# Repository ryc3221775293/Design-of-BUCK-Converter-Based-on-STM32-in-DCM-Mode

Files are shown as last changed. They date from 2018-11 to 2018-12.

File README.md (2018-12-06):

# 基于STM32的DCM模式下的BUCK变换器设计

- 本工程包括软件部分的STM32的代码以及硬件部分的Altium Designer设计的PCB
- STM32使用STM32F103RCT6并移植FreeRTOS操作系统，进行按键任务、ADC任务、PWM生成任务、PID任务的调度管理
- PCB包括控制电路STM32，驱动电路以及主电路BUCK电路

下面就两部分进行介绍：

## 5、硬件部分

### 5.1、STM32F103RCT6控制电路

Cortex-M3采用目前主流ARM V7-M架构，相比曾风靡一时的ARM V4T架构拥有更加强劲的性能，更高的代码密度，更高的性价比。Cortex-M3处理器结合多种突破性技术，在低功耗、低成本、高性能三方面具有突破性的创新，使其在这几年迅速在中低端单片机市场异军突起。

国内Cortex-M3市场，ST（意法半导体）公司的STM32无疑是最大赢家，作为Cortex-M3内核最先尝蟹的两个公司（另一个是Luminary（流明））之一，ST无论是在市场占有率，还是在技术支持方面，都是远超其他对手。在Cortex-M3芯片的选择上，STM32无疑是大家的首选。所以自从ST推出STM32之后，一股强劲的STM32学习开发风潮扑面而来。本书也因STM32的流行应运而生。

开发板选择的是STM32F103RCT6作为MCU，它拥有的资源包括：48KBSRAM、256KBFLASH、2个基本定时器、4个通用定时器、2个高级定时器、2个DMA控制器（共12个通道）、3个SPI、2个IIC、5个串口、1个USB、1个CAN、3个12位ADC、1个12位DAC、1个SDIO接口及51个通用IO口。该芯片性价比极高。

#### 5.1.1 MCU部分的原理图如图

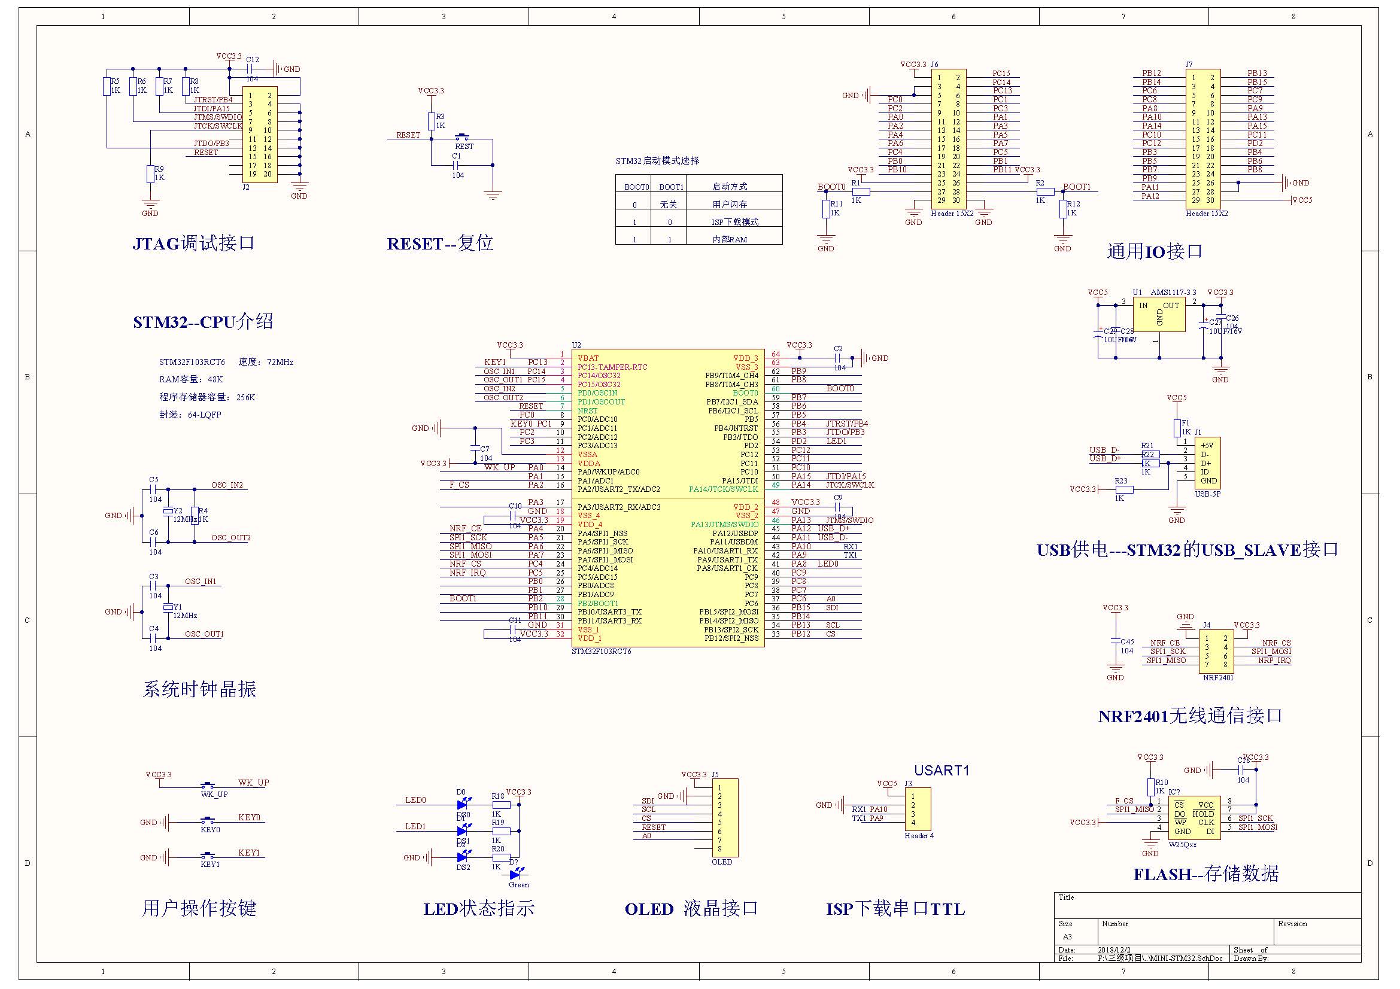
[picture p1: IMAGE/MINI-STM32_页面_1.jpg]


#### 5.1.2 PCB如图

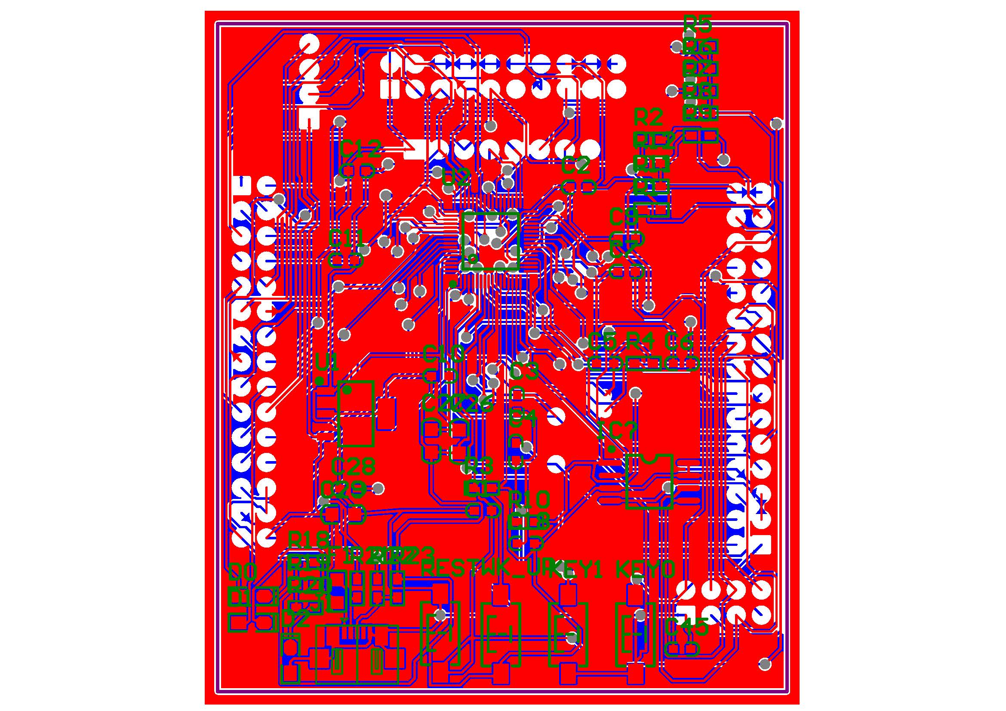
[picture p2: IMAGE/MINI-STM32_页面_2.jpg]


#### 5.1.3 PCB板的3D效果如图

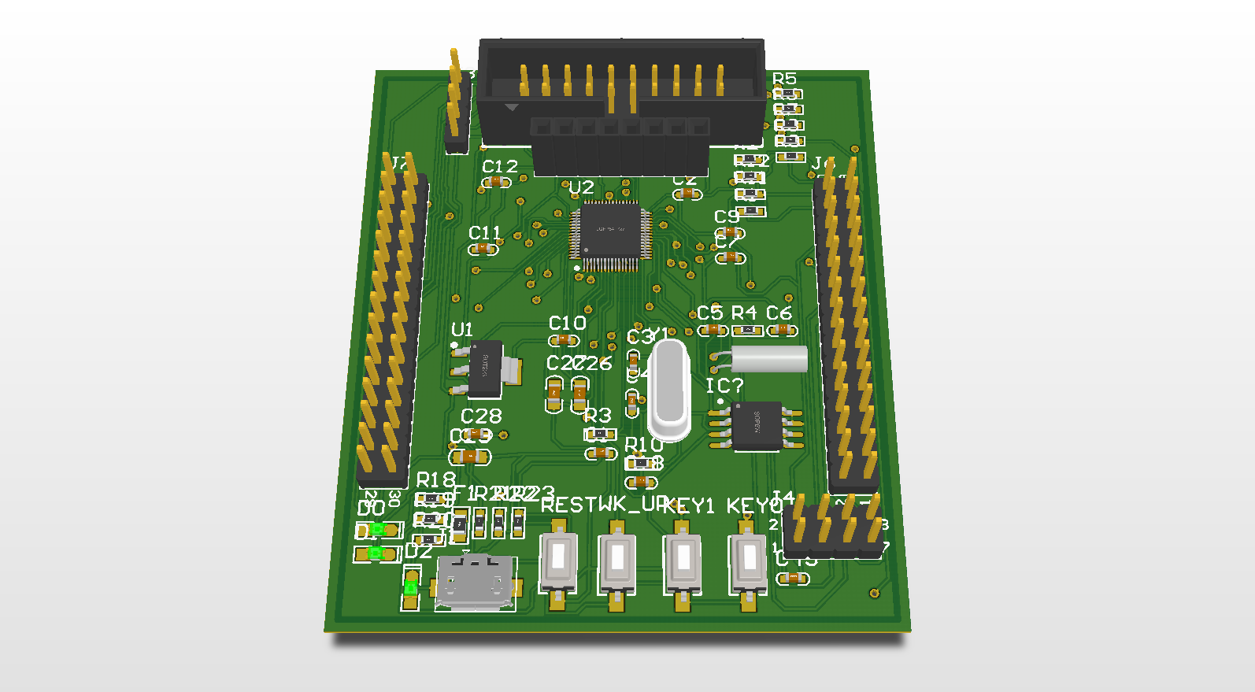
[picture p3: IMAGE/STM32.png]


#### 5.1.4 BOM报表如下

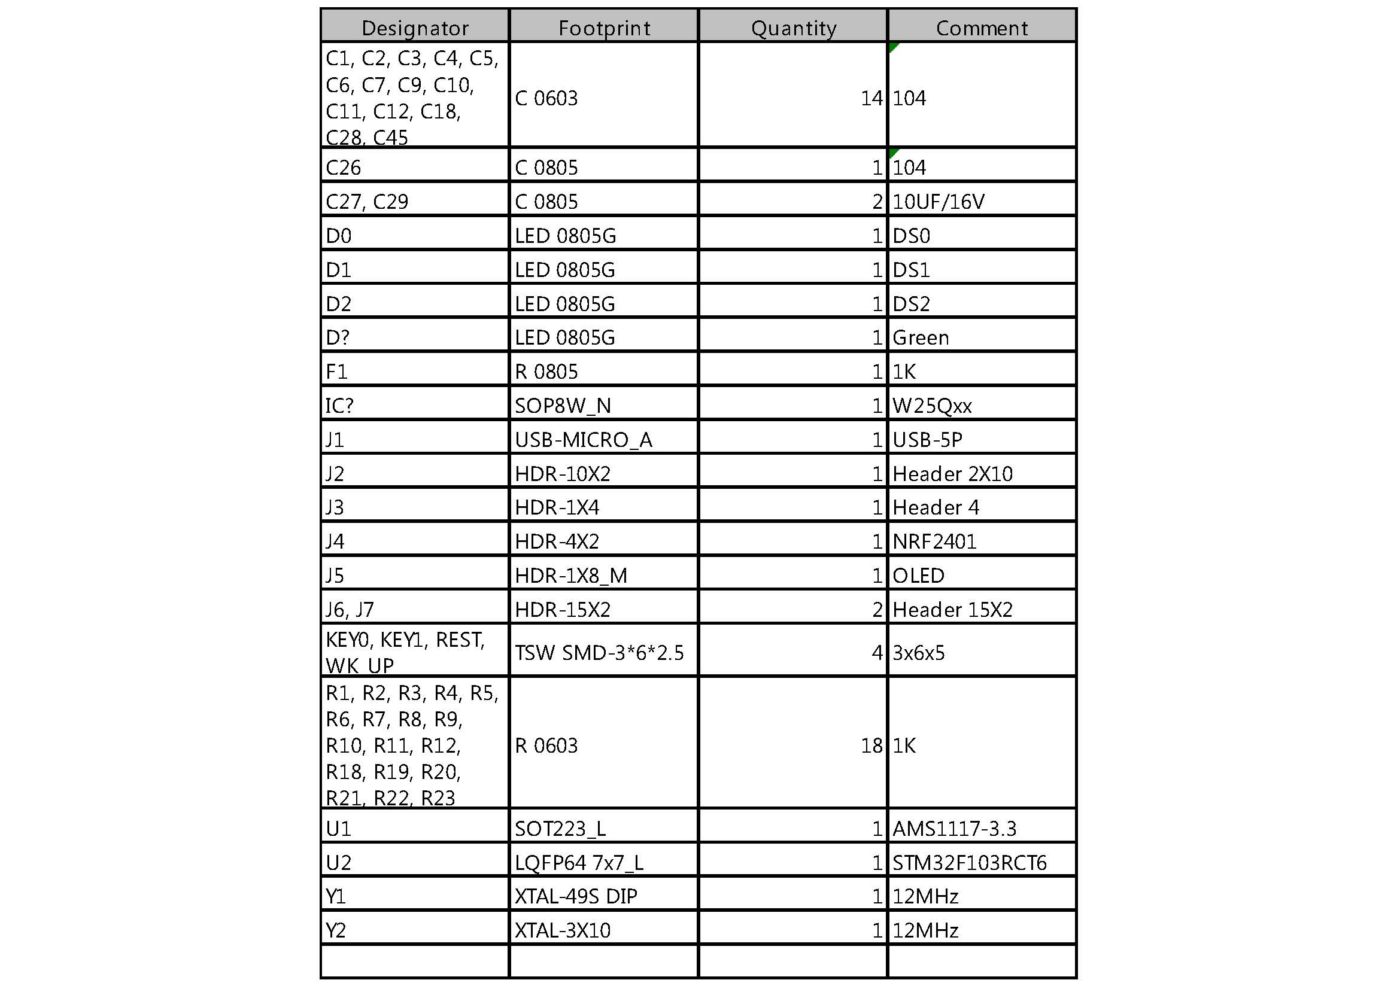
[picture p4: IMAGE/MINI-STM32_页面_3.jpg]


上图中中上部的BOOT1用于设置STM32的启动方式，其对应启动模式如下表所示：

| BOOT0 | BOOT1 | 启动模式 | 说明 |
| :---: | :---: | :---: | :---: |
| 0 | X | 用户闪存存储器 | 用户闪存存储器，也就是FLASH启动 |
| 1 | 0 | 系统存储器 |  系统存储器启动，用于串口下载 |
| 1 | 1 | SRAM启动 | SRAM启动，用于在SRAM中调试代码  |

一般情况下（即标准的ISP下载步骤）如果我们想用用串口下载代码，则必须先配置BOOT0为1，BOOT1为0，然后按复位键，最后再通过程序下载代码，下载完以后又需要将BOOT0设置为GND，以便每次复位后都可以运行用户代码。

#### 5.1.5 JTAG部分电路如下图：

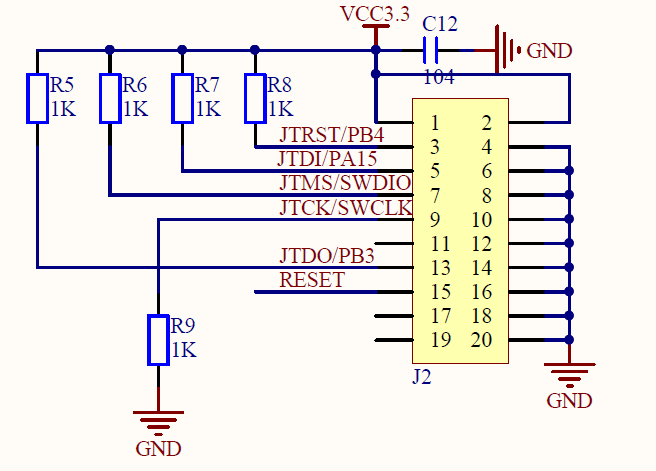
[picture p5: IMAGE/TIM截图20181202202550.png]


这里采用的是标准的JTAG接法，但是STM32还有SWD接口，SWD只需要最少2根线（SWCLK和SWDIO）就可以下载并调试代码了，这同我们使用串口下载代码差不多，而且速度更快，能调试。所以建议在设计产品的时候，可以留出SWD来下载调试代码，而摒弃JTAG。STM32的SWD接口与JTAG是共用的，只要接上JTAG，你就可以使用SWD模式了（其实SWD并不需要JTAG这么多线），JLINK V8/JLINKV7ULINK2以及STLINK等都支持SWD。这里，我们使用SWD模式。

#### 5.1.6 按键

STM32开发板总共有3个按键，其原理图如下：

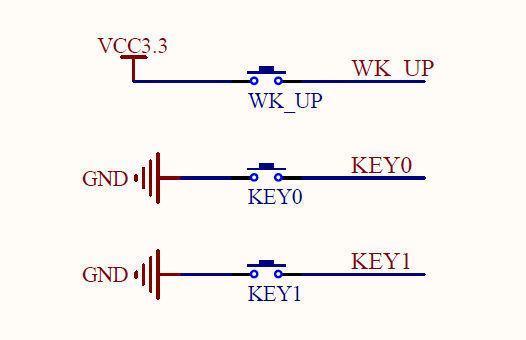
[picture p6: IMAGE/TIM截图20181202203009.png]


KEY0和KEY1用作普通按键输入，分别连接在PC1和PC13上，WKUP按键连接到PA0（STM32的WKUP引脚），它除了可以用作普通输入按键外，还可以用作STM32的唤醒输入。

#### 5.1.7 LED 

STM32开发板上总共有3个LED，其原理图如下：

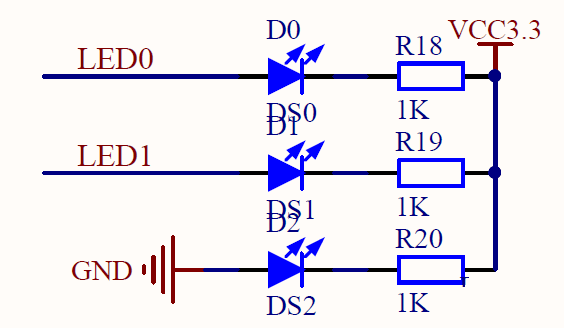
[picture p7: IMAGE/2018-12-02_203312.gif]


其中D2是开发板电源指示灯。LED0和LED1分别接在PA8和PD2上，PA8还可以通过TIM1的通道1的PWM输出来控制D0的亮度。

#### 5.1.8 无线模块
STM32 开发板板载了NRF24L01无线模块的接口。该接口用来连接NRF24L01等2.4G无线模块，从而实现开发板与其他设备的无线数据传输（注意：NRF24L01不能和蓝牙/WIFI连接）。NRF24L01无线模块的最大传输速度可以达到2Mbps，传输距离最大可以到30米左右（空旷地，无干扰）。有了这个接口，我们就可以做无线通信，以及其他很多的相关应用了。这部分原理图如下：

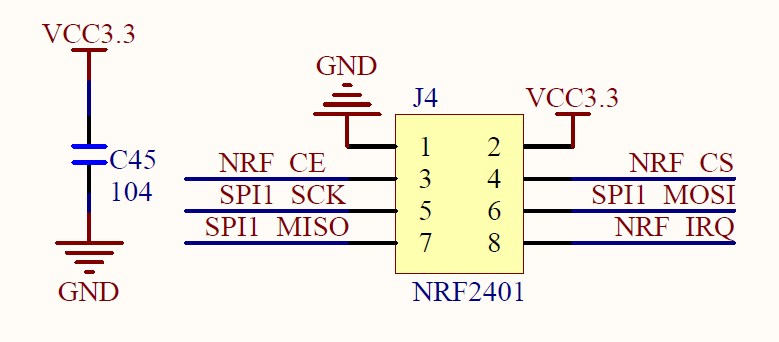
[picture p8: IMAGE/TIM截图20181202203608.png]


#### 5.1.9 SPI FLASH 

STM32开发板载有SPIFLASH芯片W25Q64，该芯片的容量为8M字节，其原理图如下：

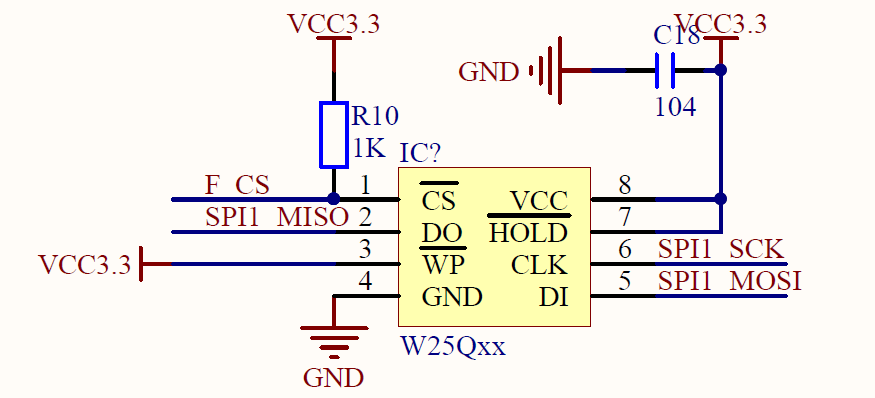
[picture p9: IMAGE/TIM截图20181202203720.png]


#### 5.1.10 USB、电源
开发板的供电部分还引出了5V（VOUT2）和3.3V（VOUT1）的排针，可以用来为外部设备提供电源或者从外部引入电源，这在很多时候是非常有用的，有时候你突然要一个3.3V的电源，但找半天就是没这样的电源，而我们的板子则可直接向外部提供3.3V电源，有了它，你就可以给外部设备提供3.3V、5V电源了。注意电流不能太大！
开发板的USB接口（USB）通过独立的MiniUSB头引出，不和USB转串口（USB232）共用，这样不但可以同时使用，还可以给系统提供更大的电流。
这几个部分的原理图如下：

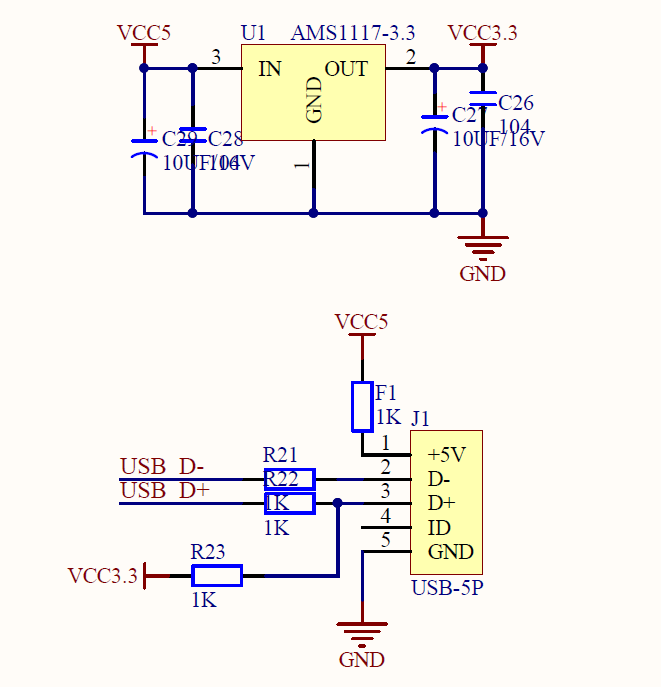
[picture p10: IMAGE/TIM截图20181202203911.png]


### 5.2、驱动电路

#### 5.2.1 驱动电路原理图如下

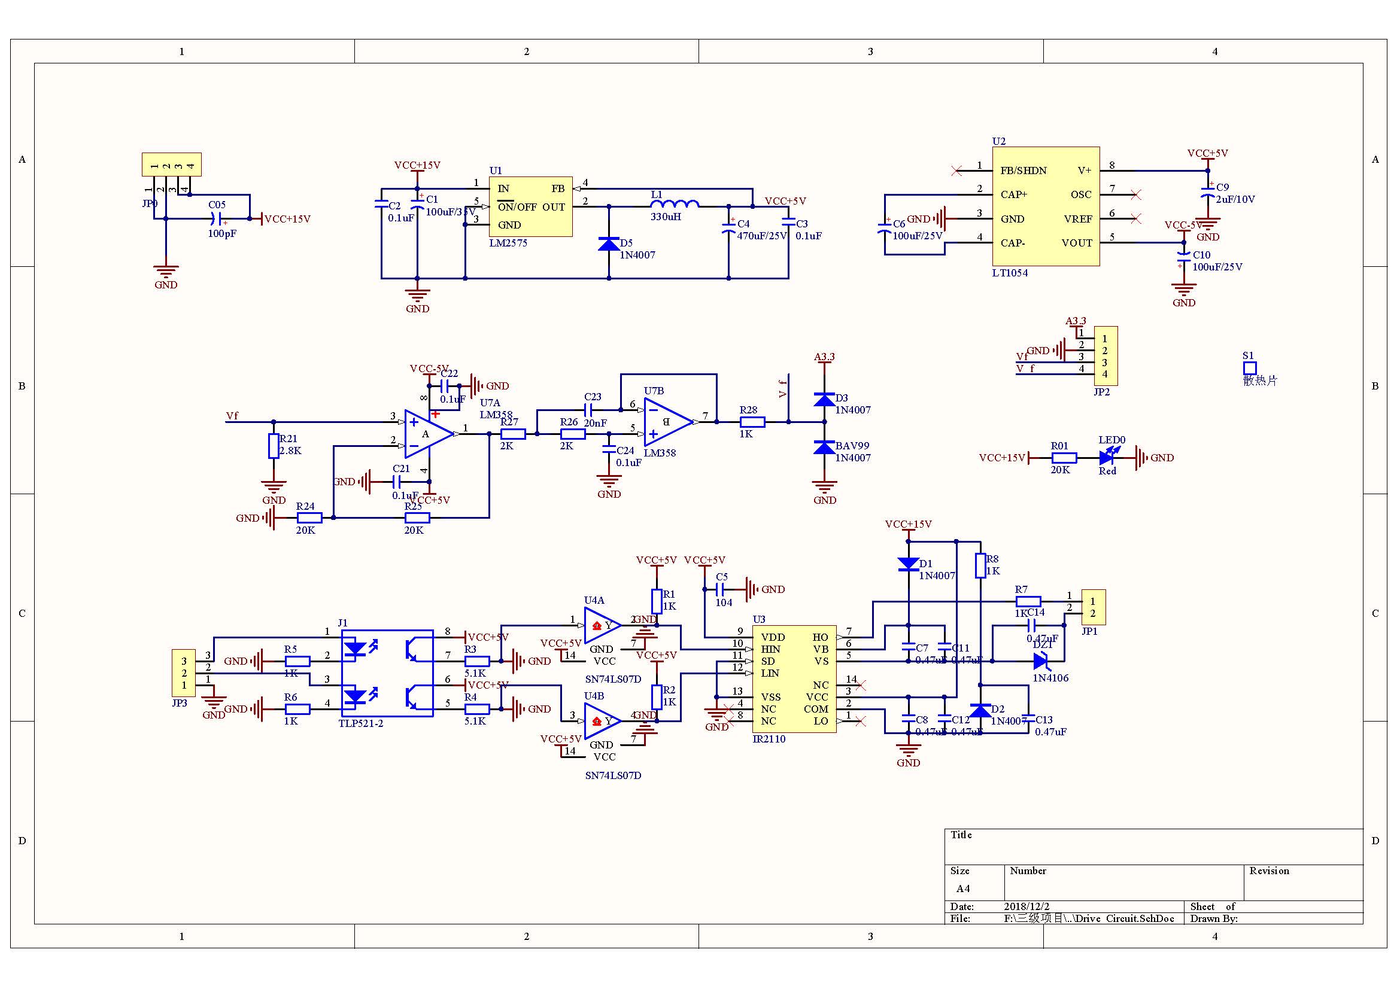
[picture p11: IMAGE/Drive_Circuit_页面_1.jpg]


#### 5.2.2 PCB如下

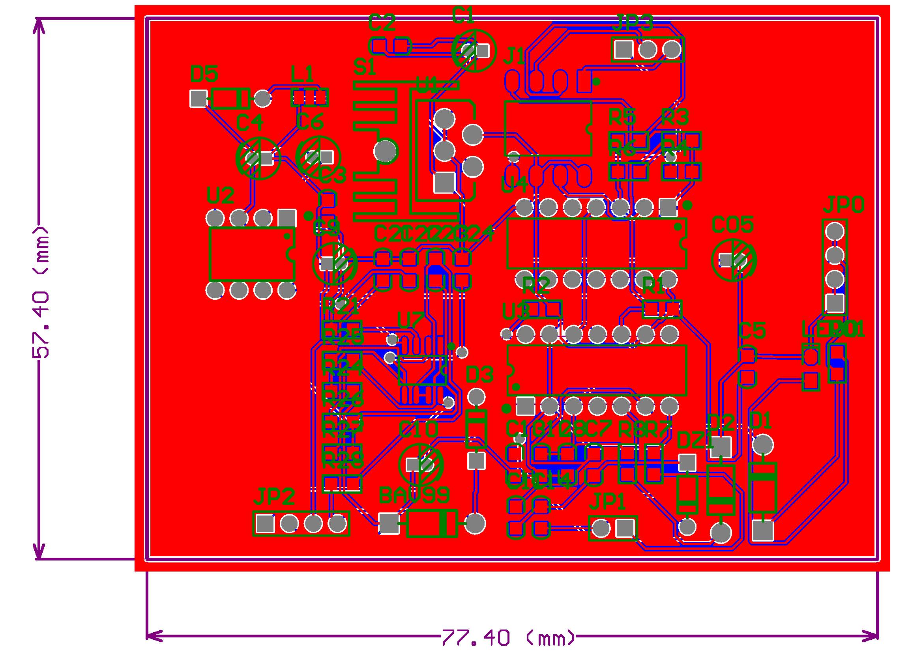
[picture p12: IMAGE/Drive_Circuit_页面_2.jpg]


#### 5.2.3 3D效果图如下

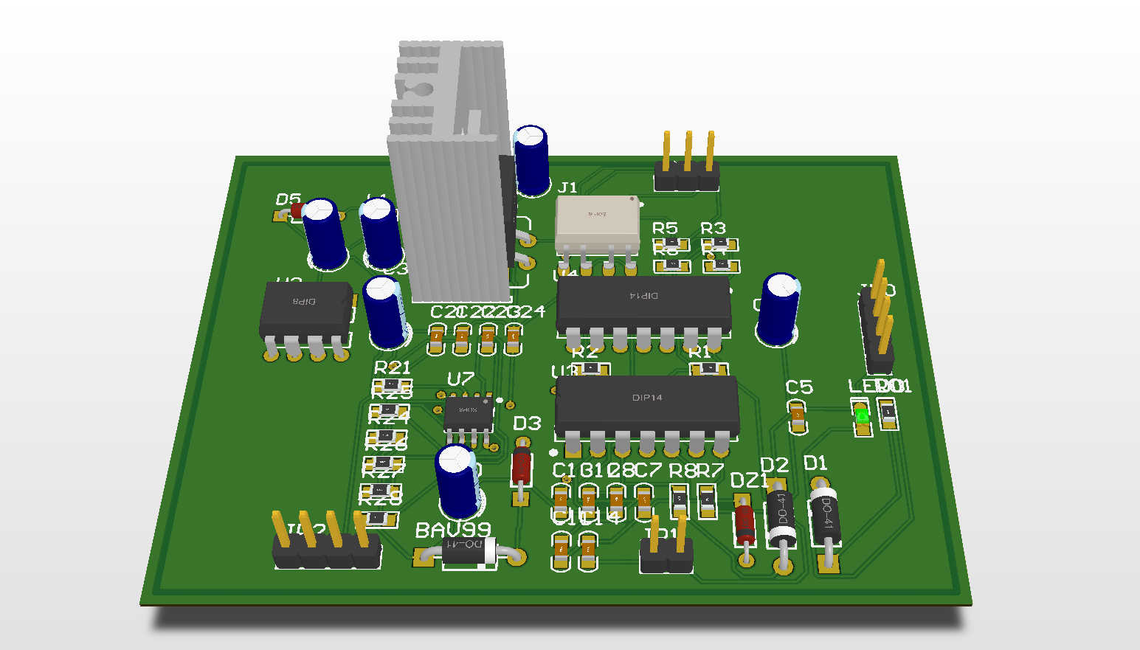
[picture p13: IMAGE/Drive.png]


#### 5.2.4 BOM报表如下

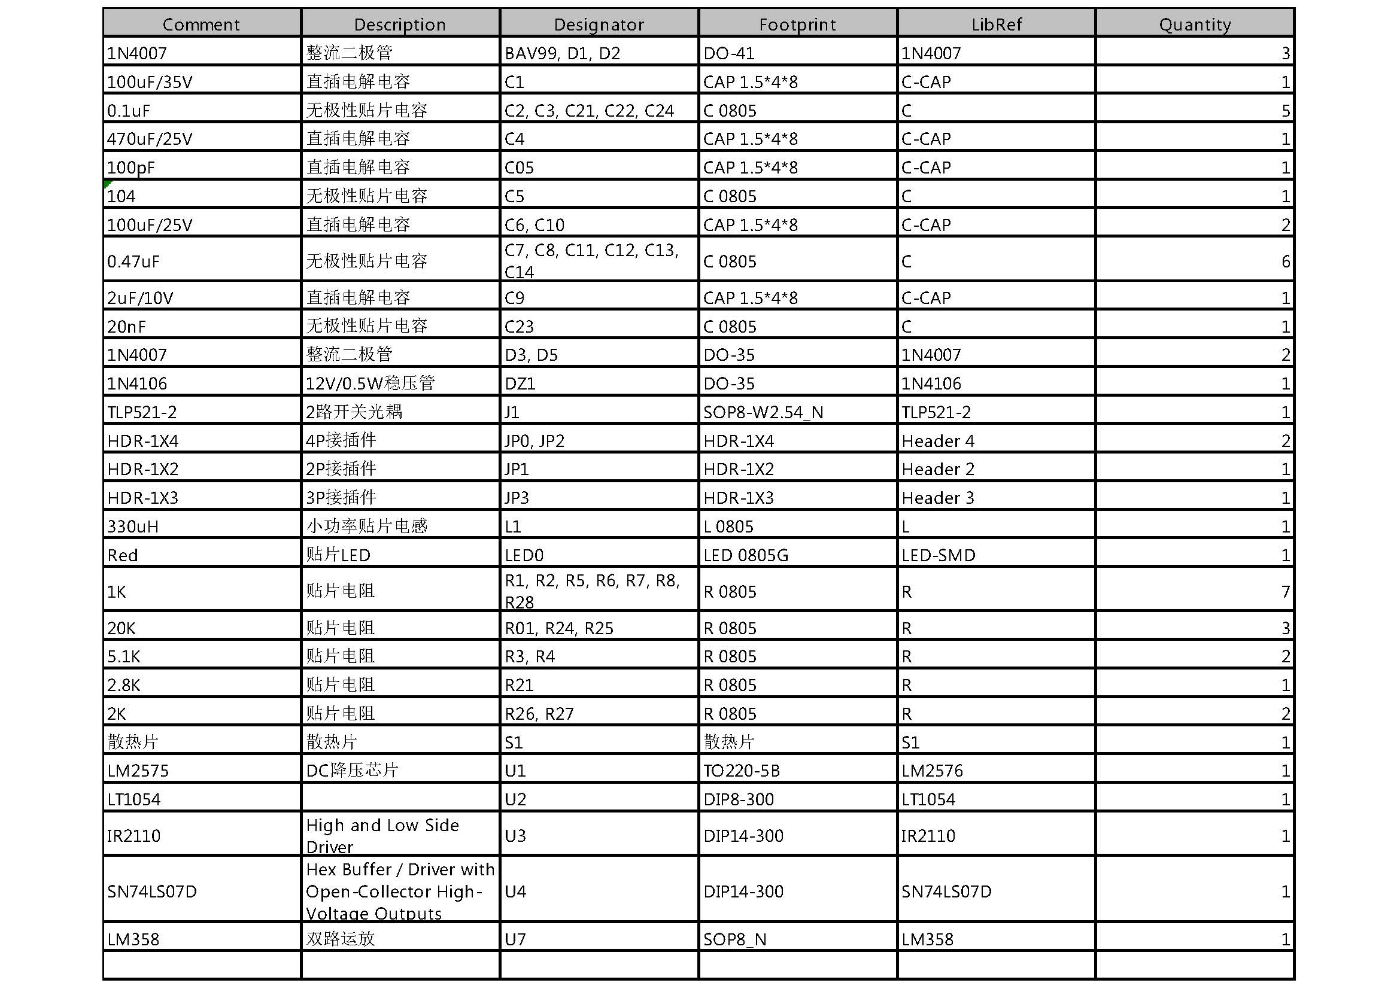
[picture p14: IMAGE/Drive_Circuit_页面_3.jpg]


#### 5.2.5 电压检测电路

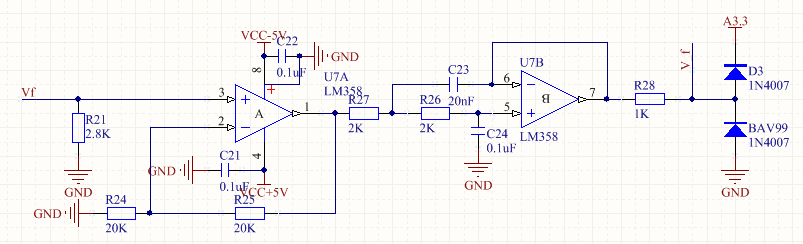
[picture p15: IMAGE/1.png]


将输出电压经过运放·358放大2倍，送入滤波电路后，进行电压限幅后送入单片机AD通道。因为输出电压一直为正，运放不会产生负压，所以358采用单电源供电，减少了-5V电源的产生电路。

#### 5.2.6 驱动电路

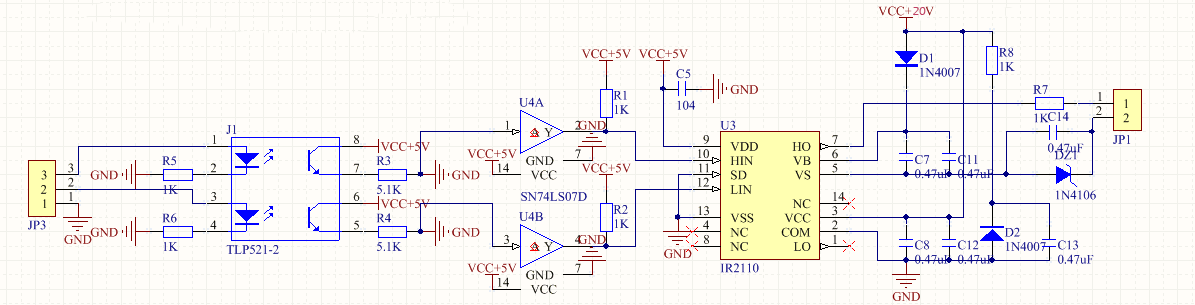
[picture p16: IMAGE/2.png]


我们在单片机的AD输出端口与IR2110外围模拟电路之间添加了TLP521光耦隔离，增强电路的安全性，减小电压的干扰。

另外，IR2110的不足是不能产生负偏压。在大功率IGBT驱动场合，各路驱动电源独立，集成驱动器一般都能产生-5 V负压，用于增强IGBT关断的可靠性，防止由于密勒效应而造成误导通。IR2110器件内部虽不能产生负压，但可通过外加无源器件产生负压。

在驱动电路中增加由电容和5V稳压管组成的负压电路。其工作原理为：电源电压Vcc为20V。在上电期间，电源通过R8为C13充电，C13保持5V电压。HIN输入高电平时，HO输出20V，加在VG1的电压为15 V。当HIN为低电平时，HO输出0 V，VG1电压为-5V。选择的C13，C14要大于IGBT栅极输入寄生电容Ciss。自举电容充电电路中的二极管D1必须是快恢复二极管，以保证在有限时间内快速导通。

#### 5.2.7 与模拟系统对比

数字系统采用单片机控制，电路需要添加隔离电路，相比较模拟系统的3525芯片及其外围电路，成本较高；而在闭环的PI调试环节，数字系统只需要更改程序中的PI参数，相比较模拟系统更改电位器的电阻值而言，更加的方便快捷。

### 5.3、主电路

#### 5.3.1 主电路原理图如下

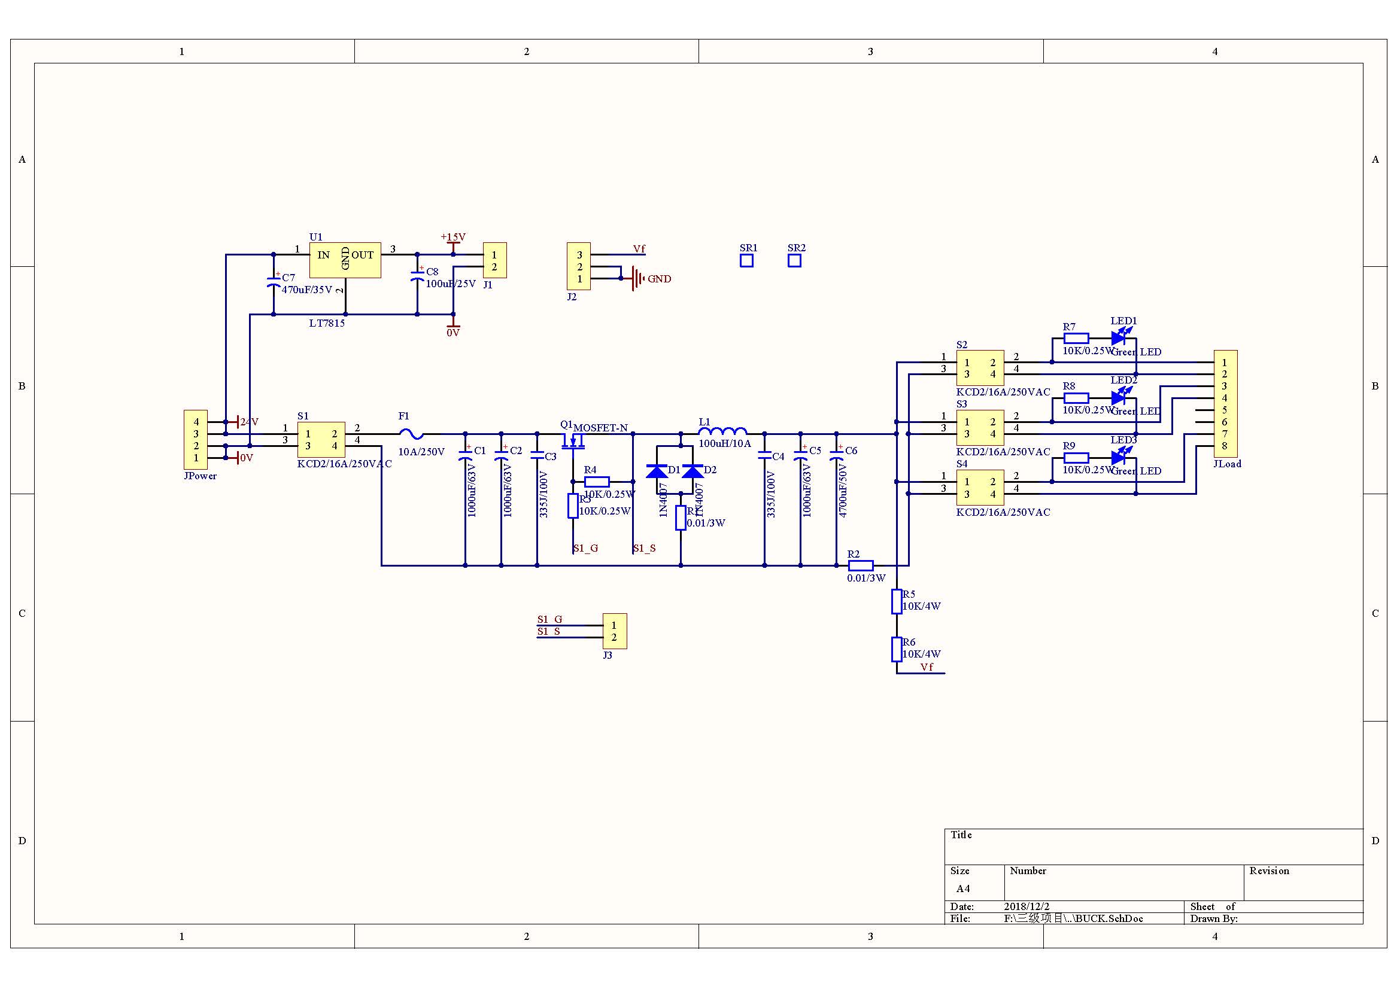
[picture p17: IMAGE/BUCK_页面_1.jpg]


#### 5.3.2 PCB如下

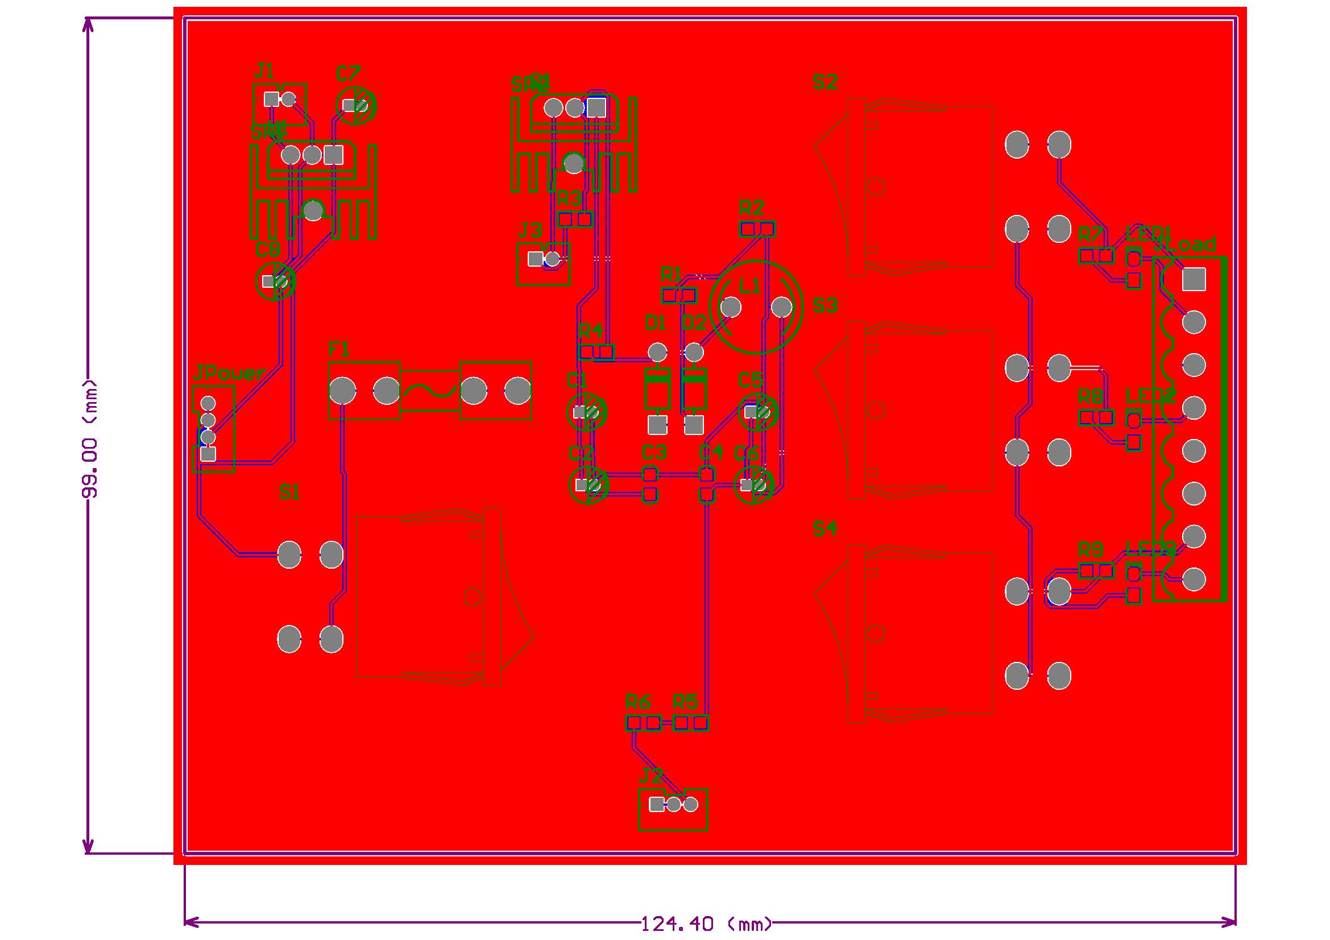
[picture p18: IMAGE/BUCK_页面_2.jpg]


#### 5.3.3 3D效果图如下

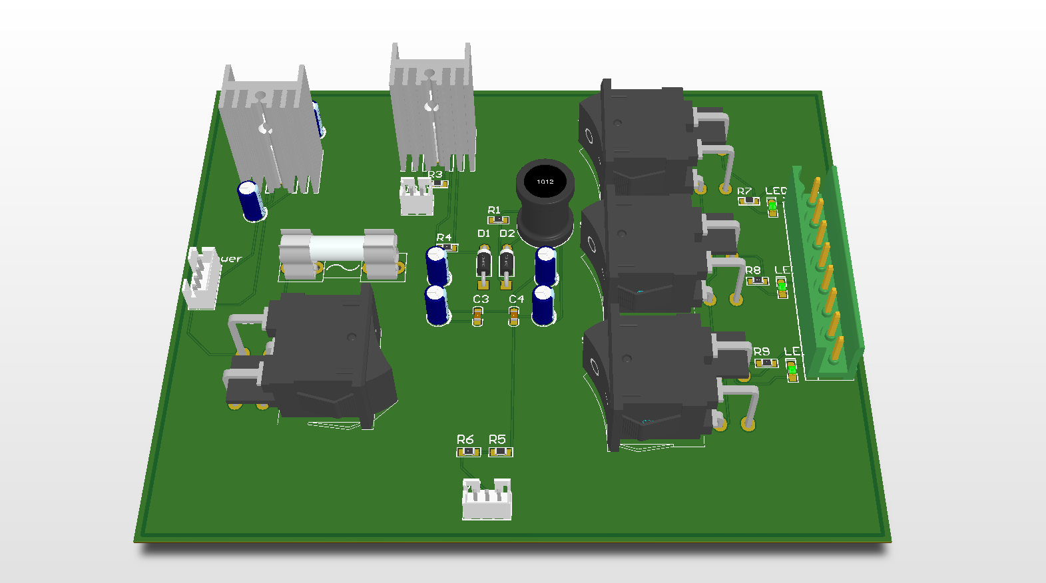
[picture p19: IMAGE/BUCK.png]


#### 5.3.4BOM报表如下

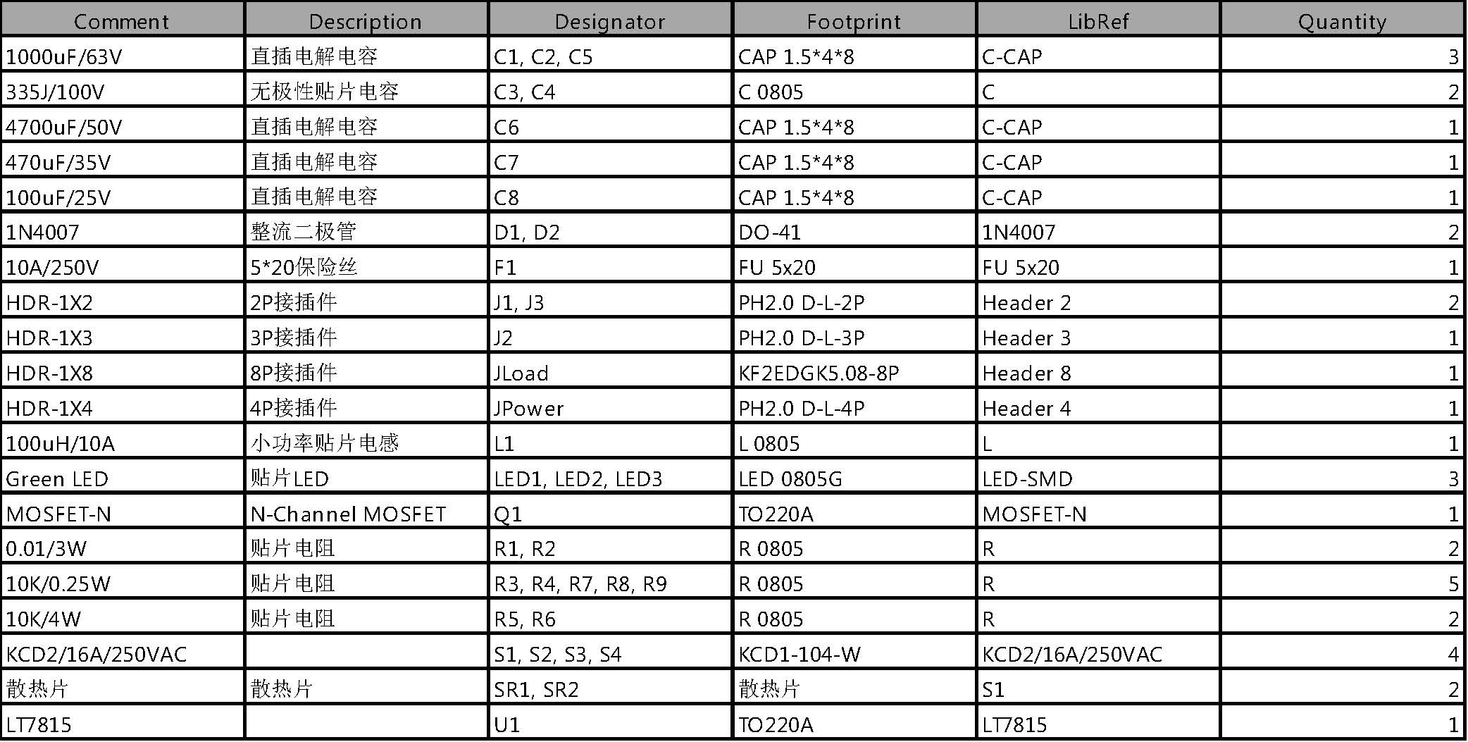
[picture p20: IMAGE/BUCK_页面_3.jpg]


### 5.4、UART 串口屏幕

串口屏定义就是，带串口控制的液晶屏就是串口屏了

详细定义：一套由单片机或PLC带控制器的显示方案，显示方案中的通讯部分由串口通讯，UART串口或者SPI串口等；它由显示驱动板、外壳、LCD液晶显 示屏三部分构成。接收用户单片机串口发送过来的指令，完成在LCD上绘图的所有操作。

#### 5.4.1 发展：

市面上， 2010年前初期版本的串口屏，都是简单的通过一个上位机软件来进行界面下载，然后发送命令过去把各种需要显示的界面显示出来，以达到所需要的显示效果，触摸方面仅支持上传坐标。

2014年发展的版本中，串口都已经形成了一个产业链，串口屏 功能非常强大，如一些串口屏带组态功能，各样功能都不再是简单的使用图片来做的粗糙操作，界面操作上越来越接近一些手机的显示。

未来的发展中，串口屏将会出现各种版本，如无线通讯版本，系统组网等等各种强大的功能，只有我们想不到的。

#### 5.4.2 应用：

广泛应用于工业自动化、电力、电信、环保、医疗、金融、石油、化工、交通、能源、地质、冶金、公共查询与监控等数十个行业和领域，其中，在某些军工及航天领域，凭借可靠、稳定的产品性能已被列入合格供应商名录。完全杜绝部分控制器存在的雪花、乱码、时序不兼容、工作温度范围窄等问题。

配套使用软件：

各个厂家各有不同的配套软件，软件上可以实现各种复杂功能，操作简单方便，部分厂家中配套有虚拟串口屏，可以直接通过软件来直接评估实体屏实现的功能，节约生产成本。

通过配套的组态软件，拥有界面设计所需要的所有控件，用户单片机只要编写一点点代码就可以完成界面设计，真正体现“零代码”

#### 5.4.3 产品特点

1、使用字符串指令

字符串指令比十六进制指令更方便开发，提升工程师的工作效率，使用字符串指令的源代码更易读，使用字符串指令在以后查阅单片机代码时会更清楚代码含义。

2、数据结构精简

产品使用指令结构如下：字符串指令+结束符

3、产品使用“C语言”指令

产品直接使用“C语言”指令，同行其他产品使用“汇编”指令。C语言指令比汇编语言更易读写，开发更方便。

4、控件属性赋值支持简易运算

比如j0控件的val属性赋值通常情况下是这么写j0.val=10
使用运算方式可以这么写：j0.val=j0.val+10
也可以这么写：j0.val=j0.val/2+10
还可以这么写：j0.val=j1.val-j0.val"2+dim（dim是系统变量）

5、屏幕固件自动升级

上位软件编译出来的资源文件就包含了最新的显示模组固件。任何功能性的升级或者bug修复，只需要使用最新的上位软件，编译出资源文件后下载到显示模组，显示模组固件立刻自动升级。上位软件有自动更新功能，只要电脑网络畅通，电脑防火墙没有隔离的软件，每次启动软件的时候软件检测到新版本会提示是否立即升级。

#### 5.4.4 功能简介

+ I/O接口：通过软件配置可以吧I/O配置成输入状态或输出状态。另外我们的产品/O可以绑定控件使用。

+ 支持通讯接口：TTL、RS232、RS485、CAN女触摸类型：电容触摸、电阻触摸、无触摸

+ 通电进入工作状态无需任何初始化设置

+ 提供用户数据存储空间（EEPROM）产品结构可根据客户需求进行定制

+ 可通过串口指令调整背光

+ 可通过串口指令画图

+ 支持RTC功能

+ 横竖可控

#### 5.4.5 原理图如下

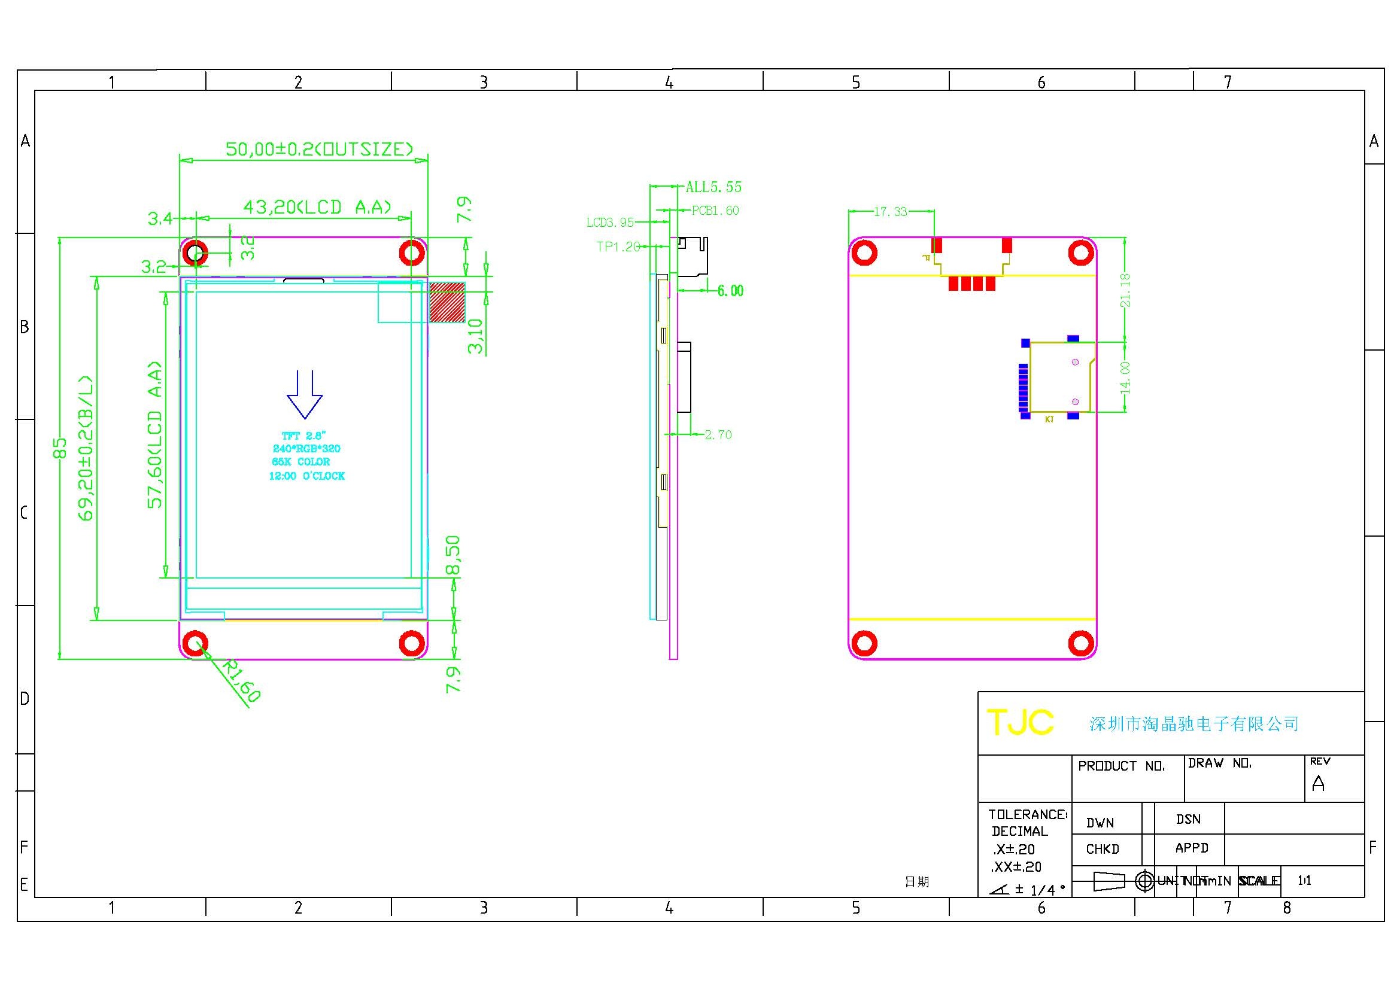
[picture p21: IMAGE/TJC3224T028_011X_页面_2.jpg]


## 6、软件部分

### 6.1 FreeRTOS简介

我们看一下FreeRTOS的名字，可以分为两部分：Free和RTOS，Free就是免费的、自由的、不受约束的意思，RTOS全称是Real Time Operating System，中文名就是实时操作系统。可以看出FreeROTS就是一个免费的RTOS类系统。这里要注意，RTOS不是指某一个确定的系统，而是指一类系统。比如UCOS，FreeRTOS，RTX，RT-Thread等这些都是RTOS类操作系统。

操作系统允许多个任务同时运行，这个叫做多任务，实际上，一个处理器核心在某一时刻只能运行一个任务。操作系统中任务调度器的责任就是决定在某一时刻究竟运行哪个任务，任务调度在各个任务之间的切换非常快！这就给人们造成了同一时刻有多个任务同时运行的错觉。

操作系统的分类方式可以由任务调度器的工作方式决定，比如有的操作系统给每个任务分配同样的运行时间，时间到了就轮到下一个任务，Unix操作系统就是这样的。RTOS的任务调度器被设计为可预测的，而这正是嵌入式实时操作系统所需要的，实时环境中要求操作系统必须对某一个事件做出实时的响应，因此系统任务调度器的行为必须是可预测的。像FreeRTOS这种传统的RTOS类操作系统是由用户给每个任务分配一个任务优先级，任务调度器就可以根据此优先级来决定下一刻应该运行哪个任务。

FreeRTOS是RTOS系统的一种，FreeRTOS十分的小巧，可以在资源有限的微控制器中运行，当然了，FreeRTOS不仅局限于在微控制器中使用。但从文件数量上来看FreeRTOS要比UCOSII和UCOSII小的多。

### 6.2 为什么选择FreeRTOS？
上面我们说了RTOS类系统有很多，为什么要选择FreeRTOS呢？在UCOS教程中，我们说过学习RTOS首选UCOS，因为UCOS的资料很多，尤其是中文资料！但是FreeRTOS的资料少，而且大多数是英文的，我为何要选择它？原因如下：

1、FreeRTOS免费！这是最重要的一点，UCOs是要收费的，学习RTOS系统的话UCOS是首选，但是做产品的话就要考虑一下成本了。显而易见的，FreeRTOS在此时就是一个很好的选择，当然了也可以选择其他的免费的RTOS系统。

2、许多其他半导体厂商产品的SDK包就使用FreeRTOS作为其操作系统，尤其是WIFI、蓝牙这些带协议栈的芯片或模块。

3、许多软件厂商也使用FreeRTOS做本公司软件的操作系统，比如著名的TouchGFX，其所有的例程都是基于FreeRTOS操作系统的。ST公司的所有要使用到RTOS系统的例程也均采用了FreeRTOS，由此可见免费的力量啊！

4、简单，FreeRTOS的文件数量很少，这个在我们后面的具体学习中就会看到，和UCOS系统相比要少很多！

5、文档相对齐全，在FreeRTOS的官网（www.freertos.org）上可以找到所需的文档和源码，但是所有的文档都是英文版本的，而且下载pdf文档的时候是要收费的。

6、FreeRTOS被移植到了很多不同的微处理器上，比如我们使用的STM32，F1、F3、F4和最新的F7都有移植，这个极大的方便了我们学习和使用。

7、社会占有量很高，EEtimes 统计的2015年RTOS系统占有量中FreeRTOS已经跃升至第一位，如图所示。

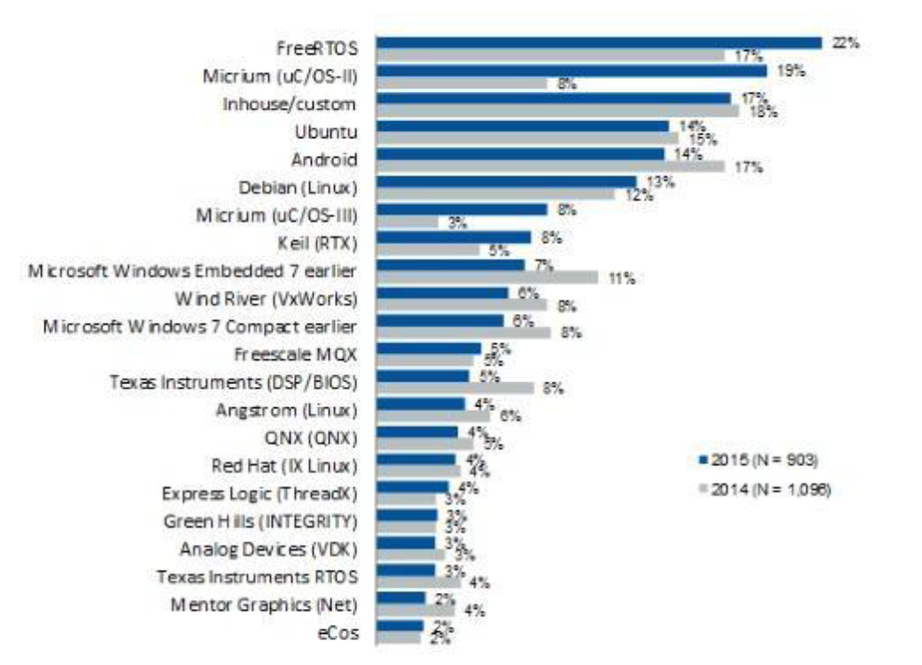
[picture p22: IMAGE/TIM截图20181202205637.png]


### 6.3 FreeRTOS特点
FreeRTOS是一个可裁剪的小型RTOS系统，其特点包括：

+ FreeRTOS的内核支持抢占式，合作式和时间片调度。

+ SafeRTOS衍生自FreeRTOS，SafeRTOS在代码完整性上相比FreeRTOS更胜一筹。
+ 提供了一个用于低功耗的Tickless模式。

+ 系统的组件在创建时可以选择动态或者静态的RAM，比如任务、消息队列、信号量、软件定时器等等。

+ 已经在超过30种架构的芯片上进行了移植。
+ FreeRTOS-MPU支持Corex-M系列中的MPU单元，如STM32F103。

+ FreeRTOS系统简单、小巧、易用，通常情况下内核占用4k-9k字节的空间。
+ 高可移植性，代码主要C语言编写。
+ 支持实时任务和协程（co-routines也有称为合作式、协同程序，本教程均成为协程）。

+ 任务与任务、任务与中断之间可以使用任务通知、消息队列、二值信号量、数值型信号量、递归互斥信号量和互斥信号量进行通信和同步。

+ 创新的事件组（或者事件标志）。
+ 具有优先级继承特性的互斥信号量。
+ 高效的软件定时器。
+ 强大的跟踪执行功能。
+ 堆栈溢出检测功能。
+ 任务数量不限。
+ 任务优先级不限。

### 6.4 FreeRTOS任务基础知识
RTOS系统的核心就是任务管理，FreeRTOS也不例外，而且大多数学习RTOS系统的工程师或者学生主要就是为了使用RTOS的多任务处理功能，初步上手RTOS系统首先必须掌握的也是任务的创建、删除、挂起和恢复等操作，由此可见任务管理的重要性。由于任务相关的知识很多，所以接下来讲解FreeRTOS的任务基础知识。

#### 6.4.1 什么是多任务系统？

以前在使用51、AVR、STM32单片机裸机（未使用系统）的时候一般都是在main 函数里面用while（1）做一个大循环来完成所有的处理，即应用程序是一个无限的循环，循环中调用相应的函数完成所需的处理。有时候我们也需要中断中完成一些处理。相对于多任务系统而言，这个就是单任务系统，也称作前后台系统，中断服务函数作为前台程序，大循环while（1）作为后台程序，如图所示：

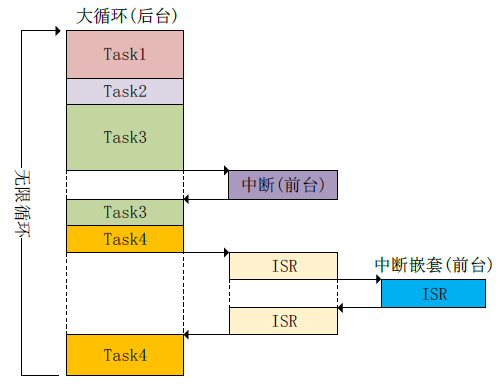
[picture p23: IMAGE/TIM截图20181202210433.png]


前后台系统的实时性差，前后台系统各个任务（应用程序）都是排队等着轮流执行，不管你这个程序现在有多紧急，没轮到你就只能等着！相当于所有任务（应用程序）的优先级都是一样的。但是前后台系统简单啊，资源消耗也少啊！在稍微大一点的嵌入式应用中前后台系统就明显力不从心了，此时就需要多任务系统出马了。

多任务系统会把一个大问题（应用）“分而治之”，把大问题划分成很多个小问题，逐步的把小问题解决掉，大问题也就随之解决了，这些小问题可以单独的作为一个小任务来处理。这些小任务是并发处理的，注意，并不是说同一时刻一起执行很多个任务，而是由于每个任务执行的时间很短，导致看起来像是同一时刻执行了很多个任务一样。多个任务带来了一个新的问题，究竟哪个任务先运行，哪个任务后运行呢？完成这个功能的东西在RTOS系统中叫做任务调度器。不同的系统其任务调度器的实现方法也不同，比如FreeRTOS是一个抢占式的实时多任务系统，那么其任务调度器也是抢占式的，运行过程如图所示：

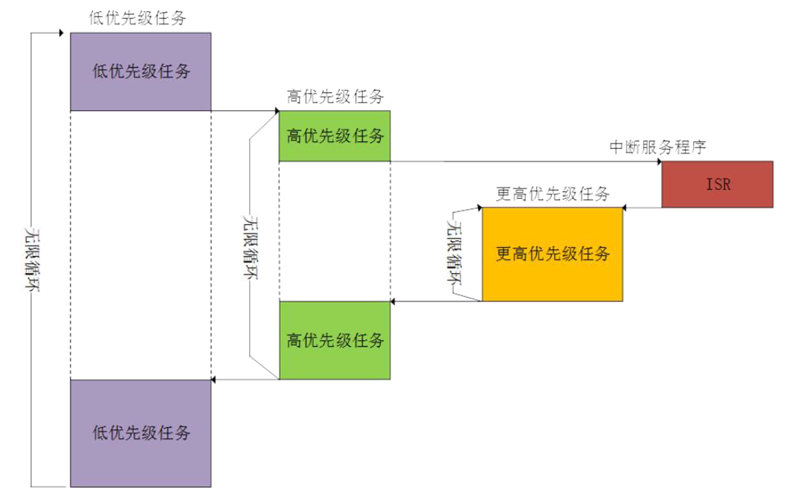
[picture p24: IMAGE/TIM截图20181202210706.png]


在图中，高优先级的任务可以打断低优先级任务的运行而取得CPU的使用权，这样就保证了那些紧急任务的运行。这样我们就可以为那些对实时性要求高的任务设置一个很高的优先级，比如自动驾驶中的障碍物检测任务等。高优先级的任务执行完成以后重新把CPU的使用权归还给低优先级的任务，这个就是抢占式多任务系统的基本原理。

#### 6.4.2 FreeRTOS任务与协程

再FreeRTOS中应用既可以使用任务，也可以使用协程（Co-Routine），或者两者混合使用。但是任务和协程使用不同的API函数，因此不能通过队列（或信号量）将数据从任务发送给协程，反之亦然。协程是为那些资源很少的MCU准备的，其开销很小，但是FreeRTOS官方已经不打算再更新协程了，所以本教程只讲解任务。

##### 任务（Task）的特性
在使用RTOS的时候一个实时应用可以作为一个独立的任务。每个任务都有自己的运行环境，不依赖于系统中其他的任务或者RTOS调度器。任何一个时间点只能有一个任务运行，具体运行哪个任务是由RTOS调度器来决定的，RTOS调度器因此就会重复的开启、关闭每个任务。任务不需要了解RTOS调度器的具体行为，RTOS调度器的职责是确保当一个任务开始执行的时候其上下文环境（寄存器值，堆栈内容等）和任务上一次退出的时候相同。为了做到这一点，每个任务都必须有个堆栈，当任务切换的时候将上下文环境保存在堆栈中，这样当任务再次执行的时候就可以从堆栈中取出上下文环境，任务恢复运行。

任务特性：

1、简单。

2、没有使用限制。

3、支持抢占

4、支持优先级

5、每个任务都拥有堆栈导致了RAM使用量增大。

6、如果使用抢占的话的必须仔细的考虑重入的问题。

##### 协程（Co-routine）的特性

协程是为那些资源很少的MCU而做的，但是随着MCU的飞速发展，性能越来越强大，现在协程几乎很少用到了！但是FreeRTOS目前还没有把协程移除的计划，但是FreeRTOS是绝对不会再更新和维护协程了，因此协程大家了解一下就行了。在概念上协程和任务是相似的，但是有如下根本上的不同：

1、堆栈使用

所有的协程使用同一个堆栈（如果是任务的话每个任务都有自己的堆栈），这样就比使用任务消耗更少的RAM。

2、调度器和优先级

协程使用合作式的调度器，但是可以在使用抢占式的调度器中使用协程。

3、宏实现

协程是通过宏定义来实现的。

4、使用限制

为了降低对RAM的消耗做了很多的限制。

#### 6.4.3 任务状态
FreeRTOS中的任务永远处于下面几个状态中的某一个：

+ 运行态
  当一个任务正在运行时，那么就说这个任务处于运行态，处于运行态的任务就是当前正在使用处理器的任务。如果使用的是单核处理器的话那么不管在任何时刻永远都只有一个任务处于运行态。·就绪态处于就绪态的任务是那些已经准备就绪（这些任务没有被阻塞或者挂起），可以运行的任务，但是处于就绪态的任务还没有运行，因为有一个同优先级或者更高优先级的任务正在运行！
+ 阻塞态
  如果一个任务当前正在等待某个外部事件的话就说它处于阻塞态，比如说如果某个任务调用了函数VTaskDelayO的话就会进入阻塞态，直到延时周期完成。任务在等待队列、信号量、事件组、通知或互斥信号量的时候也会进入阻塞态。任务进入阻塞态会有一个超时时间，当超过这个超时时间任务就会退出阻塞态，即使所等待的事件还没有来临！
+ 挂起态
  像阻塞态一样，任务进入挂起态以后也不能被调度器调用进入运行态，但是进入挂起态的任务没有超时时间。任务进入和退出挂起态通过调用函数vTaskSuspendO和xTaskResume0。
  任务状态之间的转换如图所示：

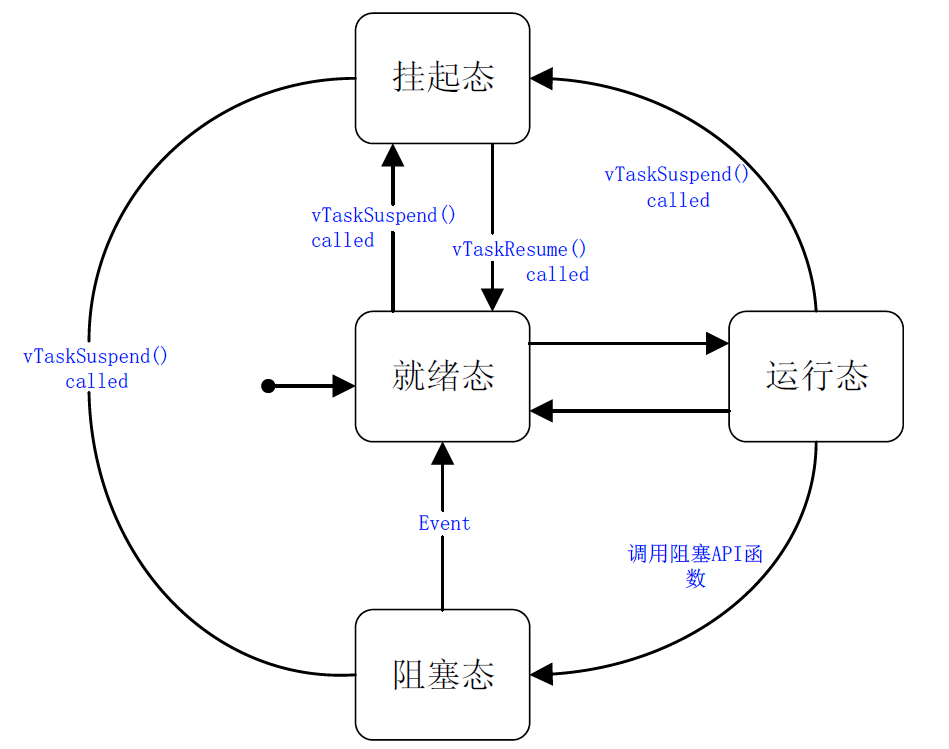
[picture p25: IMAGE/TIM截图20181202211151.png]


#### 6.4.4 任务优先级
每个任务都可以分配一个从0~（configMAX_PRIORITIES-1）的优先级，configMAX_PRIORITIES 在文件FreeRTOSConfig.h中有定义，前面我们讲解 FreeRTOS系统配置的时候已经讲过了。如果所使用的硬件平台支持类似计算前导零这样的指令（可以通过该指令选择下一个要运行的任务，Cortex-M处理器是支持该指令的），并且宏configUSE_PORT_OPTIMISED_TASK_SELECTION 也设置为了1，那么宏configMAX_PRIORITIES不能超过32！也就是优先级不能超过32级。其他情况下宏configMAX_PRIORITIES可以为任意值，但是考虑到RAM的消耗，宏configMAX_PRIORITIES最好设置为一个满足应用的最小值。

优先级数字越低表示任务的优先级越低，0的优先级最低，confieMAX_PRIORITIES-1的优先级最高。空闲任务的优先级最低，为0。

FreeRTOS调度器确保处于就绪态或运行态的高优先级的任务获取处理器使用权，换句话说就是处于就绪态的最高优先级的任务才会运行。当宏configUSE_TIME_SLICING定义为1的时候多个任务可以共用一个优先级，数量不限。默认情况下宏configUSE_TIME_SLICING在文件FreeRTOS.h中已经定义为1。此时处于就绪态的优先级相同的任务就会使用时间片轮转调度器获取运行时间。

#### 6.4.5 任务实现
在使用FreeRTOS的过程中，我们要使用函数xTaskCreate0或xTaskCreateStatic()来创建任务，这两个函数的第一个参数pxTaskCode，就是这个任务的任务函数。什么是任务函数？任务函数就是完成本任务工作的函数。我这个任务要干嘛？要做什么？要完成什么样的功能都是在这个任务函数中实现的。比如我要做个任务，这个任务要点个流水灯，那么这个流水灯的程序就是任务函数中实现的。

#### 6.4.6 任务控制块
FreeRTOS的每个任务都有一些属性需要存储，FreeRTOS把这些属性集合到一起用一个结构体来表示，这个结构体叫做任务控制块：TCB_t，在使用函数xTaskCreate0创建任务的时候就会自动的给每个任务分配一个任务控制块。在老版本的FreeRTOS中任务控制块叫做tskTCB，新版本重命名为TCBt，但是本质上还是tskTCB。

#### 6.4.7 任务堆栈
FreeRTOS 之所以能正确的恢复一个任务的运行就是因为有任务堆栈在保驾护航，任务调度器在进行任务切换的时候会将当前任务的现场（CPU寄存器值等）保存在此任务的任务堆栈中，等到此任务下次运行的时候就会先用堆栈中保存的值来恢复现场，恢复现场以后任务就会接着从上次中断的地方开始运行。

创建任务的时候需要给任务指定堆栈，如果使用的函数xTaskCreate0创建任务（动态方法）的话那么任务堆栈就会由函数xTaskCreate0自动创建，后面分析xTaskCreateO的时候会讲解。如果使用函数xTaskCreateStaticO创建任务（静态方法）的话就需要程序员自行定义任务堆栈，然后堆栈首地址作为函数的参数puxStackBuffer传递给函数。

### 6.5 FreeRTOS队列

在实际的应用中，常常会遇到一个任务或者中断服务需要和另外一个任务进行“沟通交流”，这个“沟通交流”的过程其实就是消息传递的过程。在没有操作系统的时候两个应用程序进行消息传递一般使用全局变量的方式，但是如果在使用操作系统的应用中用全局变量来传递消息就会涉及到“资源管理”的问题。FreeRTOS对此提供了一个叫做“队列”的机制来完成任务与任务、任务与中断之间的消息传递。

#### 6.5.1 队列简介
队列是为了任务与任务、任务与中断之间的通信而准备的，可以在任务与任务、任务与中断之间传递消息，队列中可以存储有限的、大小固定的数据项目。任务与任务、任务与中断之间要交流的数据保存在队列中，叫做队列项目。队列所能保存的最大数据项目数量叫做队列的长度，创建队列的时候会指定数据项目的大小和队列的长度。由于队列用来传递消息的，所以也称为消息队列。FreeRTOS中的信号量的也是依据队列实现的！所以有必要深入的了解FreeRTOS的队列。

##### 数据存储
通常队列采用先进先出（FIFO）的存储缓冲机制，也就是往队列发送数据的时候（也叫入队）永远都是发送到队列的尾部，而从队列提取数据的时候（也叫出队）是从队列的头部提取的。但是也可以使用LIFO的存储缓冲，也就是后进先出，FreeRTOS中的队列也提供了LIFO的存储缓冲机制。

数据发送到队列中会导致数据拷贝，也就是将要发送的数据拷贝到队列中，这就意味着在队列中存储的是数据的原始值，而不是原数据的引用（即只传递数据的指针），这个也叫做值传递。学过UCOS的应该知道，UCOS的消息队列采用的是引用传递，传递的是消息指针。

采用引用传递的话消息内容就必须一直保持可见性，也就是消息内容必须有效，那么局部变量这种可能会随时被删掉的东西就不能用来传递消息，但是采用引用传递会节省时间啊！因为不用进行数据拷贝。

采用值传递的话虽然会导致数据拷贝，会浪费一点时间，但是一旦将消息发送到队列中原始的数据缓冲区就可以删除掉或者覆写，这样的话这些缓冲区就可以被重复的使用。FreeRTOS中使用队列传递消息的话虽然使用的是数据拷贝，但是也可以使用引用来传递消息啊，我直接往队列中发送指向这个消息的地址指针不就可以了！这样当我要发送的消息数据太大的时候就可以直接发送消息缓冲区的地址指针，比如在网络应用环境中，网络的数据量往往都很大的，采用数据拷贝的话就不现实。

1、多任务访问

队列不是属于某个特别指定的任务的，任何任务都可以向队列中发送消息，或者从队列中提取消息。

2、出队阻塞

当任务尝试从一个队列中读取消息的时候可以指定一个阻塞时间，这个阻塞时间就是当任务从队列中读取消息无效的时候任务阻塞的时间。出队就是就从队列中读取消息，出队阻塞是针对从队列中读取消息的任务而言的。比如任务A用于处理串口接收到的数据，串口接收到数据以后就会放到队列Q中，任务A从队列Q中读取数据。但是如果此时队列Q是空的，说明还没有数据，任务A这时候来读取的话肯定是获取不到任何东西，那该怎么办呢？任务A现在有三种选择，一：二话不说扭头就走，二：要不我在等等吧，等一会看看，说不定一会就有数据了，三：死等，死也要等到你有数据！选哪一个就是由这个阻塞时间决定的，这个阻塞时间单位是时钟节拍数。阻塞时间为0的话就是不阻塞，没有数据的话就马上返回任务继续执行接下来的代码，对应第一种选择。如果阻塞时间为0～portMAXDELAY，当任务没有从队列中获取到消息的话就进入阻塞态，阻塞时间指定了任务进入阻塞态的时间，当阻塞时间到了以后还没有接收到数据的话就退出阻塞态，返回任务接着运行下面的代码，如果在阻塞时间内接收到了数据就立即返回，执行任务中下面的代码，这种情况对应第二种选择。当阻塞时间设置为portMAX_DELAY的话，任务就会一直进入阻塞态等待，直到接收到数据为止！这个就是第三种选择。

3、入队阻塞

入队说的是向队列中发送消息，将消息加入到队列中。和出队阻塞一样，当一个任务向队列发送消息的话也可以设置阻塞时间。比如任务B向消息队列Q发送消息，但是此时队列Q是满的，那肯定是发送失败的。此时任务B就会遇到和上面任务A一样的问题，这两种情况的处理过程是类似的，只不过一个是向队列Q发送消息，一个是从队列Q读取消息而已。

4、队列操作过程图示

下面几幅图简单的演示了一下队列的入队和出队过程。

+ 创建队列



图中任务A要向任务B发送消息，这个消息是x变量的值。首先创建一个队列，并且指定队列的长度和每条消息的长度。这里我们创建了一个长度为4的队列，因为要传递的是x值，而x是个int类型的变量，所以每条消息的长度就是int类型的长度，在STM32中就是4字节，即每条消息是4个字节的。

+ 向队列发送第一个消息



图中任务A的变量x值为10，将这个值发送到消息队列中。此时队列剩余长度就是3了。前面说了向队列中发送消息是采用拷贝的方式，所以一旦消息发送完成变量x就可以再次被使用，赋其他的值。

+ 向队列发送第二个消息



图中任务A又向队列发送了一个消息，即新的x的值，这里是20。此时队列剩余长度为2。

+ 从队列中读取消息



### 6.6 代码解析

#### mian.c（主函数） 

```c
//引用头文件
#include "sys.h"
#include "delay.h"
#include "usart.h"
#include "led.h"
#include "key.h"
#include "HMI.h"
#include "timer.h"
#include "adc.h"
#include "pid.h"
#include <math.h> 
#include "malloc.h"
#include "string.h"
#include "FreeRTOS.h"
#include "task.h"
#include "queue.h"

//开始任务参数设置
//任务优先级
#define START_TASK_PRIO		1
//任务堆栈大小	
#define START_STK_SIZE 		256  
//任务句柄
TaskHandle_t StartTask_Handler;
//任务函数
void start_task(void *pvParameters);

//ADC任务参数设置
//任务优先级
#define ADC_TASK_PRIO		3
//任务堆栈大小	
#define ADC_STK_SIZE 		256  
//任务句柄
TaskHandle_t ADCTask_Handler;
//任务函数
void adc_task(void *pvParameters);

//按键任务参数设置
//任务优先级
#define KEYPROCESS_TASK_PRIO 2
//任务堆栈大小	 
#define KEYPROCESS_STK_SIZE  128 
//任务句柄
TaskHandle_t Keyprocess_Handler;
//任务函数
void Keyprocess_task(void *pvParameters);

//PID调节任务参数设置
//任务优先级
#define PID_TASK_PRIO 4
//任务堆栈大小	 
#define PID_STK_SIZE  256 
//任务句柄
TaskHandle_t PID_Handler;
//任务函数
void pid_task(void *pvParameters);

//消息队列参数设置，按键与ADC值的队列都设置为20长度
#define KEYMSG_Q_NUM    20		//按键消息队列的数量 
#define MESSAGE_Q_NUM   20 	//发送数据的消息队列的数量
QueueHandle_t Key_Queue;   		//按键值消息队列句柄
QueueHandle_t Message_Queue;	//信息队列句柄

//进入低功耗模式前需要处理的事情
//ulExpectedIdleTime：低功耗模式运行时间
void PreSleepProcessing(uint32_t ulExpectedIdleTime)
{
	//关闭某些低功耗模式下不使用的外设时钟，此处只是演示性代码
	RCC_APB2PeriphClockCmd(RCC_APB2Periph_GPIOB,DISABLE);
	RCC_APB2PeriphClockCmd(RCC_APB2Periph_GPIOC,DISABLE);
	RCC_APB2PeriphClockCmd(RCC_APB2Periph_GPIOD,DISABLE);
	RCC_APB2PeriphClockCmd(RCC_APB2Periph_GPIOE,DISABLE);
	RCC_APB2PeriphClockCmd(RCC_APB2Periph_GPIOF,DISABLE);
	RCC_APB2PeriphClockCmd(RCC_APB2Periph_GPIOG,DISABLE);
}

//退出低功耗模式以后需要处理的事情
//ulExpectedIdleTime：低功耗模式运行时间
void PostSleepProcessing(uint32_t ulExpectedIdleTime)
{
	//退出低功耗模式以后打开那些被关闭的外设时钟，此处只是演示性代码
	RCC_APB2PeriphClockCmd(RCC_APB2Periph_GPIOB,ENABLE);
	RCC_APB2PeriphClockCmd(RCC_APB2Periph_GPIOC,ENABLE);
	RCC_APB2PeriphClockCmd(RCC_APB2Periph_GPIOD,ENABLE);
	RCC_APB2PeriphClockCmd(RCC_APB2Periph_GPIOE,ENABLE);
	RCC_APB2PeriphClockCmd(RCC_APB2Periph_GPIOF,ENABLE);
	RCC_APB2PeriphClockCmd(RCC_APB2Periph_GPIOG,ENABLE);	              
}

int main(void)
{
	NVIC_PriorityGroupConfig(NVIC_PriorityGroup_4);//设置系统中断优先级分组4	 
	delay_init();	    				//延时函数初始化	 
	uart_init(9600);					//初始化串口
	LED_Init();							//LED初始化
	PID_init();							//PID初始化
	KEY_Init();							//按键初始化
	TIM3_PWM_Init(1439,0);	 			//TIM3初始化，不分频。PWM频率=72000000/1440=50Khz
	Adc_Init();		  					//ADC初始化	
	my_mem_init(SRAMIN);            	//初始化内部内存池
	
	//创建开始任务
    xTaskCreate((TaskFunction_t )start_task,            //任务函数
                (const char*    )"start_task",          //任务名称
                (uint16_t       )START_STK_SIZE,        //任务堆栈大小
                (void*          )NULL,                  //传递给任务函数的参数
                (UBaseType_t    )START_TASK_PRIO,       //任务优先级
                (TaskHandle_t*  )&StartTask_Handler);   //任务句柄              
    vTaskStartScheduler();          //开启任务调度
}

//开始任务任务函数
void start_task(void *pvParameters)
{
    taskENTER_CRITICAL();           //进入临界区
	
	//创建消息队列
	Key_Queue=xQueueCreate(KEYMSG_Q_NUM,sizeof(u16));        //创建消息Key_Queue
    Message_Queue=xQueueCreate(MESSAGE_Q_NUM,sizeof(u16)); //创建消息Message_Queue,队列项长度是串口接收缓冲区长度
	
    //创建TASK1任务
    xTaskCreate((TaskFunction_t )adc_task,             
                (const char*    )"adc_task",           
                (uint16_t       )ADC_STK_SIZE,        
                (void*          )NULL,                  
                (UBaseType_t    )ADC_TASK_PRIO,        
                (TaskHandle_t*  )&ADCTask_Handler);  
				
	//创建TASK2任务
    xTaskCreate((TaskFunction_t )Keyprocess_task,     
                (const char*    )"keyprocess_task",   
                (uint16_t       )KEYPROCESS_STK_SIZE,
                (void*          )NULL,
                (UBaseType_t    )KEYPROCESS_TASK_PRIO,
                (TaskHandle_t*  )&Keyprocess_Handler);
				
    //创建TASK3任务
    xTaskCreate((TaskFunction_t )pid_task,     
                (const char*    )"pid_task",   
                (uint16_t       )PID_STK_SIZE,
                (void*          )NULL,
                (UBaseType_t    )PID_TASK_PRIO,
                (TaskHandle_t*  )&PID_Handler); 
    vTaskDelete(StartTask_Handler); //删除开始任务
    taskEXIT_CRITICAL();            //退出临界区
}
//ADC任务函数
void adc_task(void *pvParameters)
{
	u16 adcx,flo;
	
	BaseType_t err;									//定义错误返回接收句柄
	while(1)
	{
		adcx=Get_Adc_Average(ADC_Channel_1,10);		//ADC通道1采样10次并取平均值
		flo = (int)adcx*134.3/4096;				//串口屏要显示的实际电压值
		CurveCommand(1,0,flo);						//将电压值通过串口发送到串口屏幕显示
		if ((Message_Queue!=NULL) && (adcx))		//如果队列创建成功并且ADC采集到数据
		{
			err=xQueueSend(Message_Queue,&adcx,10);	//将数据装入队列，如果队列已满最多等10个时钟节拍，否则放弃本次入队操作
            if(err==errQUEUE_FULL)   				//如果入队失败
            {
                //printf("队列Message_Queue已满，数据发送失败!\r\n");
            }
		}
		vTaskDelay(10);                           	//延时10ms，也就是10个时钟节拍	
	}
}

//Keyprocess_task函数
void Keyprocess_task(void *pvParameters)
{
	u8 key;
	u16 pwm=0;
    BaseType_t err;
	while(1)
	{
		key=KEY_Scan(0);            				//扫描按键
		switch(key)
		{
			case WKUP_PRES:		//KEY_UP控制pwm值加90
				pwm += 90;
				break;
			case KEY1_PRES:		//KEY1控制pwm值加180
				pwm += 10;
				break;
			case KEY0_PRES:		//KEY0控制pwm值减90
				pwm = 556;
				break;
		}
		if (pwm>1440)			//限制pwm的值不能超过1440
		{
			pwm = 1440;
		}
		NumberCommand(0,(int)pwm*100/1440);		//串口屏幕显示当前输出电压的值
		NumberCommand(1,(int)pwm*24/1440);		//串口屏幕显示当前输出占空比的值
		if((Key_Queue!=NULL)&&(pwm!=0))   		//消息队列Key_Queue创建成功,并且按键被按下
        {
            err=xQueueSend(Key_Queue,&pwm,10);
            if(err==errQUEUE_FULL)   			//如果入队失败
            {
                //printf("队列Key_Queue已满，数据发送失败!\r\n");
            }
        }
		vTaskDelay(10);                           //延时10ms，也就是10个时钟节拍	
	}
	
}

//PID_task函数
void pid_task(void *pvParameters)
{
	u16 adcx,pwm;
	extern PID V_PID;
	while(1)
	{		
		if(Message_Queue!=NULL && Key_Queue!=NULL)	//如果按键队列和ADC消息队列都创建成功
        {
            if(xQueueReceive(Message_Queue,&adcx,portMAX_DELAY) && xQueueReceive(Key_Queue,&pwm,portMAX_DELAY))//请求消息Message_Queue和Key_Queue
            {
				//闭环
				V_PID.setpulse = pwm*4096/1440;		//按键给定值
				V_PID.backpulse = adcx/2;		//电压反馈值
				PWM_VAL1=V_PIDCalc(&V_PID);
				PWM_VAL2=V_PIDCalc(&V_PID);
				//开环
				//PWM_VAL1=pwm;
				//PWM_VAL2=pwm;
			}
		}
		vTaskDelay(10);      //延时10ms，也就是10个时钟节拍
	}
}

```

#### PID.c（PID调节代码）

```c
#include "pid.h"

PID V_PID;
void PID_init(void)
{	
  	V_PID.setpulse = 0 ;	      	//电压设定值
  	V_PID.backpulse = 0 ;			//电压反馈值		
  	V_PID.last_error = 0 ;	 
  	V_PID.pre_error = 0 ;	  
  	V_PID.P = Pv;
  	V_PID.I = Iv;
  	V_PID.D = Dv;	
  	V_PID.motorout = 0 ;		    //控制输出值
}

unsigned int V_PIDCalc( PID *pp )	//按照课本给定的PID公式进行操作
{
    int error;
    
	error = pp->setpulse - pp->backpulse;

  	pp->motorout +=( int) (pp->P*(error-pp->last_error) + pp->I*error + pp->D*(error-2*pp->last_error+pp->pre_error));
 		
 	pp->pre_error = pp->last_error;	 
 	pp->last_error = error;
    	
    if( pp->motorout >= D_MAX) 		
		   pp->motorout = D_MAX;		
    else if( pp->motorout <= D_MIN)	//电压PID，防止调节最低溢出 
		   pp->motorout = D_MIN;			
  	
  	return (pp->motorout);			// 返回预调节占空比
}
```

#### pid.h（PID调节代码）

```	c
#ifndef __PID_H
#define __PID_H

#include "delay.h"
#include "stm32f10x.h"

/////////////////PID调节////////////////////////////////////////////////////
#define  Pv  0.1  	//0.6//0.1		     振荡 0.05	 振荡至稳定0.1		   
#define  Iv  0.5	//0.08					      0.04			   0.03		   
#define  Dv  0

#define D_MAX 620	//占空比输出最大值
#define D_MIN 0 	//占空比输出最小值
//定义PID
typedef struct PID		
{
	int setpulse;		    //设定值
  	int backpulse;			//反馈值
	int last_error;  	
	int pre_error;	
	float P;		    	
	float I;		    
	float D;		    						
	int motorout;	  		//控制输出值	
}PID;

void PID_init(void);
unsigned int V_PIDCalc( PID *pp );		

#endif
```

#### timer.c（定时器与PWM代码）

```c
#include "timer.h"
#include "led.h"
#include "usart.h"
   	  
//TIM3 PWM部分初始化 
//PWM输出初始化
//arr：自动重装值
//psc：时钟预分频数
void TIM3_PWM_Init(u16 arr,u16 psc)
{  
	GPIO_InitTypeDef GPIO_InitStructure;
	TIM_TimeBaseInitTypeDef  TIM_TimeBaseStructure;
	TIM_OCInitTypeDef  TIM_OCInitStructure;

	RCC_APB1PeriphClockCmd(RCC_APB1Periph_TIM3, ENABLE);	//使能定时器3时钟
 	RCC_APB2PeriphClockCmd(RCC_APB2Periph_GPIOA  , ENABLE);  //使能GPIOA模块时钟

   //设置该引脚为复用输出功能,输出TIM3 CH1的PWM脉冲波形	GPIOA.6
	GPIO_InitStructure.GPIO_Pin = GPIO_Pin_6|GPIO_Pin_7; //TIM_CH2
	GPIO_InitStructure.GPIO_Mode = GPIO_Mode_AF_PP;  //复用推挽输出
	GPIO_InitStructure.GPIO_Speed = GPIO_Speed_50MHz;
	GPIO_Init(GPIOA, &GPIO_InitStructure);//初始化GPIO
 
   //初始化TIM3
	TIM_TimeBaseStructure.TIM_Period = arr; //设置在下一个更新事件装入活动的自动重装载寄存器周期的值
	TIM_TimeBaseStructure.TIM_Prescaler =psc; //设置用来作为TIMx时钟频率除数的预分频值 
	TIM_TimeBaseStructure.TIM_ClockDivision = 0; //设置时钟分割:TDTS = Tck_tim
	TIM_TimeBaseStructure.TIM_CounterMode = TIM_CounterMode_Up;  //TIM向上计数模式
	TIM_TimeBaseInit(TIM3, &TIM_TimeBaseStructure); //根据TIM_TimeBaseInitStruct中指定的参数初始化TIMx的时间基数单位
	
	//初始化TIM3 Channel2 PWM模式	 
	TIM_OCInitStructure.TIM_OCMode = TIM_OCMode_PWM1; //选择定时器模式:TIM脉冲宽度调制模式2
 	TIM_OCInitStructure.TIM_OutputState = TIM_OutputState_Enable; //比较输出使能
	TIM_OCInitStructure.TIM_OCPolarity = TIM_OCPolarity_High; //输出极性:TIM输出比较极性高
	TIM_OC1Init(TIM3, &TIM_OCInitStructure);  //根据T指定的参数初始化外设TIM3 OC1

	TIM_OC1PreloadConfig(TIM3, TIM_OCPreload_Enable);  //使能TIM3在CCR1上的预装载寄存器
 	//上面两句中的OC1确定了是channle几，要是OC2则是channel 2  
	TIM3->CCR1 = 0;	    //初始化占空比

	TIM_OC2Init(TIM3, &TIM_OCInitStructure);  //根据T指定的参数初始化外设TIM3 OC1
	TIM_OC2PreloadConfig(TIM3, TIM_OCPreload_Enable);  //使能TIM3在CCR1上的预装载寄存器
    TIM3->CCR2 = 0;

	TIM_Cmd(TIM3, ENABLE);  //使能TIM3
	
}
```

#### adc.c（ADC采样代码）

```c
 #include "adc.h"
 #include "delay.h"	   
		   
//初始化ADC
//这里我们仅以规则通道为例
//我们默认将开启通道0~3																	 
void  Adc_Init(void)
{ 	
	ADC_InitTypeDef ADC_InitStructure; 
	GPIO_InitTypeDef GPIO_InitStructure;

	RCC_APB2PeriphClockCmd(RCC_APB2Periph_GPIOA |RCC_APB2Periph_ADC1	, ENABLE );	  //使能ADC1通道时钟
 
	RCC_ADCCLKConfig(RCC_PCLK2_Div6);   //设置ADC分频因子6 72M/6=12,ADC最大时间不能超过14M

	//PA1 作为模拟通道输入引脚                         
	GPIO_InitStructure.GPIO_Pin = GPIO_Pin_1|GPIO_Pin_2;
	GPIO_InitStructure.GPIO_Mode = GPIO_Mode_AIN;		//模拟输入引脚
	GPIO_Init(GPIOA, &GPIO_InitStructure);	

	ADC_DeInit(ADC1);  //复位ADC1,将外设 ADC1 的全部寄存器重设为缺省值

	ADC_InitStructure.ADC_Mode = ADC_Mode_Independent;	//ADC工作模式:ADC1和ADC2工作在独立模式
	ADC_InitStructure.ADC_ScanConvMode = DISABLE;	//模数转换工作在单通道模式
	ADC_InitStructure.ADC_ContinuousConvMode = DISABLE;	//模数转换工作在单次转换模式
	ADC_InitStructure.ADC_ExternalTrigConv = ADC_ExternalTrigConv_None;	//转换由软件而不是外部触发启动
	ADC_InitStructure.ADC_DataAlign = ADC_DataAlign_Right;	//ADC数据右对齐
	ADC_InitStructure.ADC_NbrOfChannel = 1;	//顺序进行规则转换的ADC通道的数目
	ADC_Init(ADC1, &ADC_InitStructure);	//根据ADC_InitStruct中指定的参数初始化外设ADCx的寄存器   
  
	ADC_Cmd(ADC1, ENABLE);	//使能指定的ADC1
	
	ADC_ResetCalibration(ADC1);	//使能复位校准  
	 
	while(ADC_GetResetCalibrationStatus(ADC1));	//等待复位校准结束
	
	ADC_StartCalibration(ADC1);	 //开启AD校准
 
	while(ADC_GetCalibrationStatus(ADC1));	 //等待校准结束
}	

//获得ADC值
//ch:通道值 0~3
u16 Get_Adc(u8 ch)   
{
  	//设置指定ADC的规则组通道，一个序列，采样时间
	ADC_RegularChannelConfig(ADC1, ch, 1, ADC_SampleTime_239Cycles5 );	//ADC1,ADC通道,采样时间为239.5周期	  			    
  
	ADC_SoftwareStartConvCmd(ADC1, ENABLE);		//使能指定的ADC1的软件转换启动功能	
	 
	while(!ADC_GetFlagStatus(ADC1, ADC_FLAG_EOC ));//等待转换结束

	return ADC_GetConversionValue(ADC1);	//返回最近一次ADC1规则组的转换结果
}

u16 Get_Adc_Average(u8 ch,u8 times)			//采样times次并取平均值
{
	u32 temp_val=0;
	u8 t;
	for(t=0;t<times;t++)
	{
		temp_val+=Get_Adc(ch);
		delay_ms(5);
	}
	return temp_val/times;
} 	 
```

#### HMI.c（串口屏幕显示代码）

```c
#include "HMI.h"
#include "usart.h"

void CurveCommand(int ID, int channel, int value)		//串口屏幕绘图曲线指令
{
	USART_SendData(USART1, 0XFF);//向串口1发送数据	 
	while(USART_GetFlagStatus(USART1,USART_FLAG_TC)!=SET);//等待发送结束
	USART_SendData(USART1, 0XFF);//向串口1发送数据	 
	while(USART_GetFlagStatus(USART1,USART_FLAG_TC)!=SET);//等待发送结束
	USART_SendData(USART1, 0XFF);//向串口1发送数据	 
	while(USART_GetFlagStatus(USART1,USART_FLAG_TC)!=SET);//等待发送结束
	printf("add %d,%d,%d",ID,channel,value);
	while(USART_GetFlagStatus(USART1,USART_FLAG_TC)!=SET);//等待发送结束
	USART_SendData(USART1, 0XFF);//向串口1发送数据	 
	while(USART_GetFlagStatus(USART1,USART_FLAG_TC)!=SET);//等待发送结束
	USART_SendData(USART1, 0XFF);//向串口1发送数据	 
	while(USART_GetFlagStatus(USART1,USART_FLAG_TC)!=SET);//等待发送结束
	USART_SendData(USART1, 0XFF);//向串口1发送数据	 
	while(USART_GetFlagStatus(USART1,USART_FLAG_TC)!=SET);//等待发送结束
	
}
	
void NumberCommand(int ID,int num)						//串口屏幕绘制数字指令
{
	USART_SendData(USART1, 0XFF);//向串口1发送数据	 
	while(USART_GetFlagStatus(USART1,USART_FLAG_TC)!=SET);//等待发送结束
	USART_SendData(USART1, 0XFF);//向串口1发送数据	 
	while(USART_GetFlagStatus(USART1,USART_FLAG_TC)!=SET);//等待发送结束
	USART_SendData(USART1, 0XFF);//向串口1发送数据	 
	while(USART_GetFlagStatus(USART1,USART_FLAG_TC)!=SET);//等待发送结束
	printf("n%d.val=%d",ID,num);
	while(USART_GetFlagStatus(USART1,USART_FLAG_TC)!=SET);//等待发送结束
	USART_SendData(USART1, 0XFF);//向串口1发送数据	 
	while(USART_GetFlagStatus(USART1,USART_FLAG_TC)!=SET);//等待发送结束
	USART_SendData(USART1, 0XFF);//向串口1发送数据	 
	while(USART_GetFlagStatus(USART1,USART_FLAG_TC)!=SET);//等待发送结束
	USART_SendData(USART1, 0XFF);//向串口1发送数据	 
	while(USART_GetFlagStatus(USART1,USART_FLAG_TC)!=SET);//等待发送结束

}
```

#### key.c（按键代码）

```c
#include "stm32f10x.h"
#include "key.h"
#include "sys.h" 
#include "delay.h"
								    
//按键初始化函数
void KEY_Init(void) //IO初始化
{ 
 	GPIO_InitTypeDef GPIO_InitStructure;
 
 	RCC_APB2PeriphClockCmd(RCC_APB2Periph_GPIOA|RCC_APB2Periph_GPIOC,ENABLE);//使能PORTA,PORTE时钟

	GPIO_InitStructure.GPIO_Pin  = GPIO_Pin_1|GPIO_Pin_13;//KEY0-KEY1
	GPIO_InitStructure.GPIO_Mode = GPIO_Mode_IPU; //设置成上拉输入
 	GPIO_Init(GPIOC, &GPIO_InitStructure);//初始化GPIOE4,3

	//初始化 WK_UP-->GPIOA.0	  下拉输入
	GPIO_InitStructure.GPIO_Pin  = GPIO_Pin_0;
	GPIO_InitStructure.GPIO_Mode = GPIO_Mode_IPD; //PA0设置成输入，默认下拉	  
	GPIO_Init(GPIOA, &GPIO_InitStructure);//初始化GPIOA.0

}
//按键处理函数
//返回按键值
//mode:0,不支持连续按;1,支持连续按;
//0，没有任何按键按下
//1，KEY0按下
//2，KEY1按下
//3，KEY3按下 WK_UP
//注意此函数有响应优先级,KEY0>KEY1>KEY_UP!!
u8 KEY_Scan(u8 mode)
{	 
	static u8 key_up=1;//按键按松开标志
	if(mode)key_up=1;  //支持连按		  
	if(key_up&&(KEY0==0||KEY1==0||WK_UP==1))
	{
		delay_ms(10);//去抖动 
		key_up=0;
		if(KEY0==0)return KEY0_PRES;
		else if(KEY1==0)return KEY1_PRES;
		else if(WK_UP==1)return WKUP_PRES;
	}else if(KEY0==1&&KEY1==1&&WK_UP==0)key_up=1; 	    
 	return 0;// 无按键按下
}
```

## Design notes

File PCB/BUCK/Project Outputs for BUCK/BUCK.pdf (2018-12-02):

Comment | Description | Designator | Footprint | LibRef | Quantity
1000uF/63V | 直插电解电容 | C1, C2, C5 | CAP 1.5*4*8 | C-CAP | 3
335J/100V | 无极性贴片电容 | C3, C4 | C 0805 | C | 2
4700uF/50V | 直插电解电容 | C6 | CAP 1.5*4*8 | C-CAP | 1
470uF/35V | 直插电解电容 | C7 | CAP 1.5*4*8 | C-CAP | 1
100uF/25V | 直插电解电容 | C8 | CAP 1.5*4*8 | C-CAP | 1
1N4007 | 整流二极管 | D1, D2 | DO-41 | 1N4007 | 2
10A/250V | 5*20保险丝 | F1 | FU 5x20 | FU 5x20 | 1
HDR-1X2 | 2P接插件 | J1, J3 | PH2.0 D-L-2P | Header 2 | 2
HDR-1X3 | 3P接插件 | J2 | PH2.0 D-L-3P | Header 3 | 1
HDR-1X8 | 8P接插件 | JLoad | KF2EDGK5.08-8P | Header 8 | 1
HDR-1X4 | 4P接插件 | JPower | PH2.0 D-L-4P | Header 4 | 1
100uH/10A | 小功率贴片电感 | L1 | L 0805 | L | 1
Green LED | 贴片LED | LED1, LED2, LED3 | LED 0805G | LED-SMD | 3
MOSFET-N | N-Channel MOSFET | Q1 | TO220A | MOSFET-N | 1
0.01/3W | 贴片电阻 | R1, R2 | R 0805 | R | 2
10K/0.25W | 贴片电阻 | R3, R4, R7, R8, R9 | R 0805 | R | 5
10K/4W | 贴片电阻 | R5, R6 | R 0805 | R | 2
KCD2/16A/250VAC | | S1, S2, S3, S4 | KCD1-104-W | KCD2/16A/250VAC | 4
散热片 | 散热片 | SR1, SR2 | 散热片 | S1 | 2
LT7815 | | U1 | TO220A | LT7815 | 1

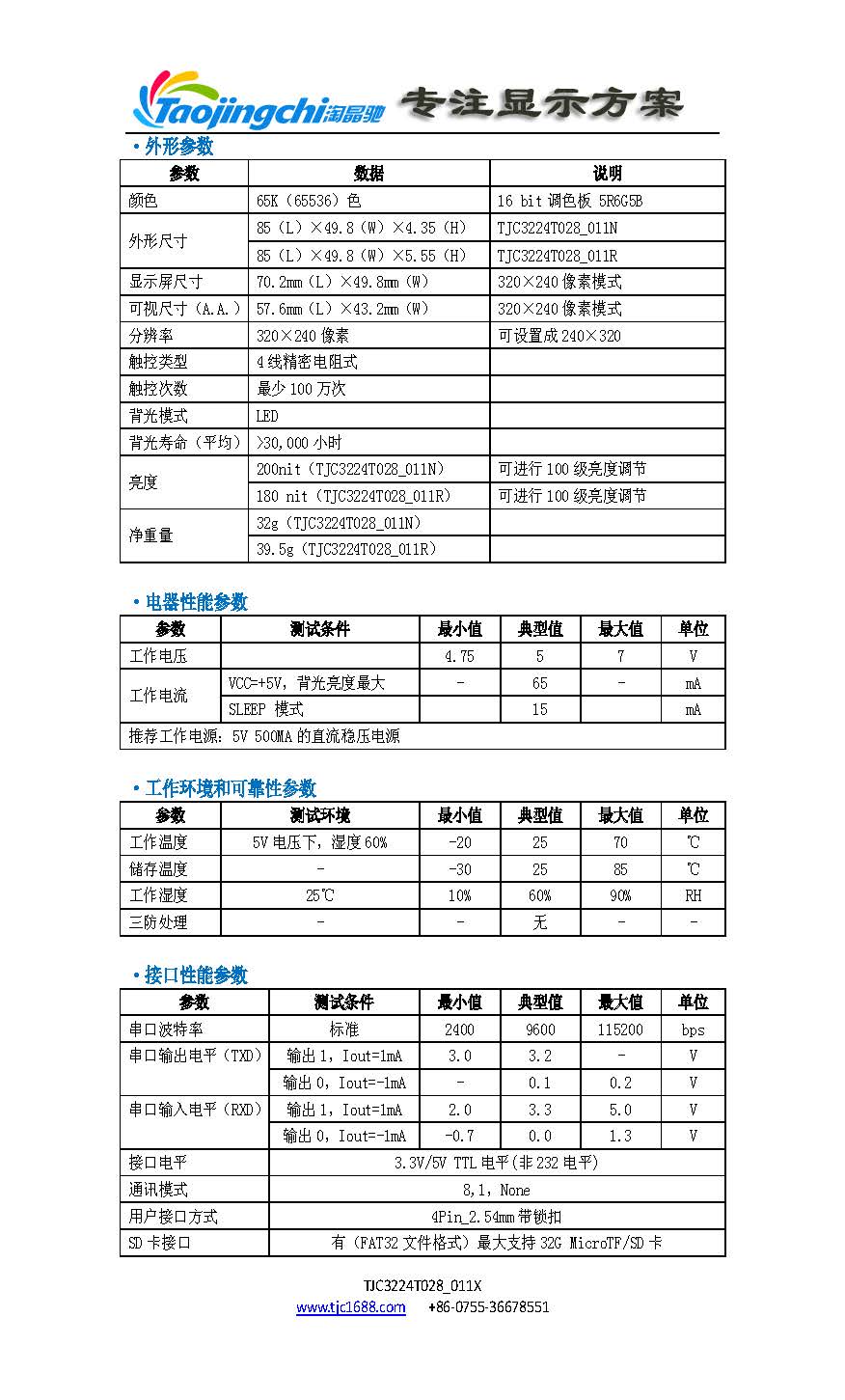
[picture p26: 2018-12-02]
IMAGE/TJC3224T028_011X_页面_3.jpg

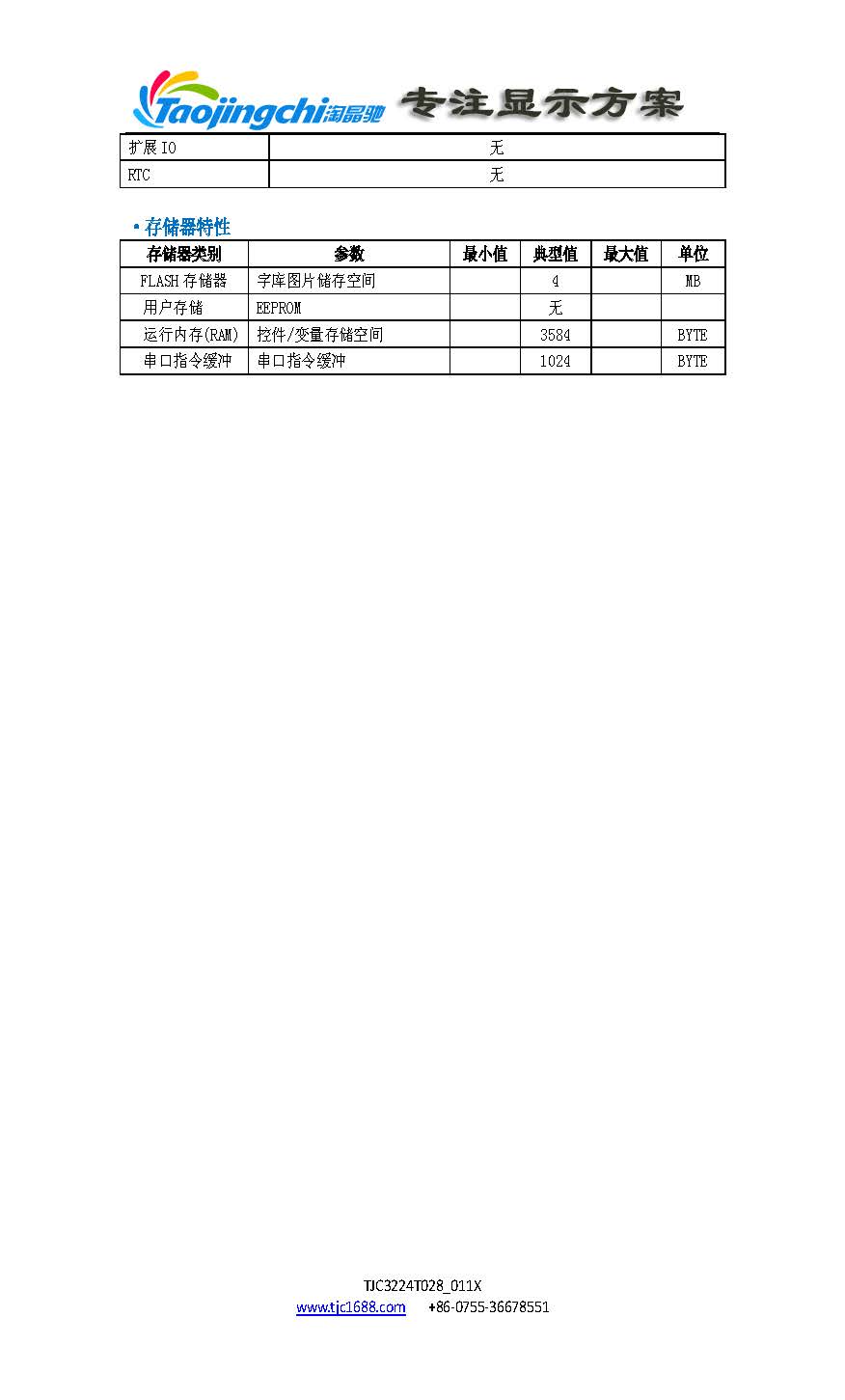
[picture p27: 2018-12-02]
IMAGE/TJC3224T028_011X_页面_4.jpg

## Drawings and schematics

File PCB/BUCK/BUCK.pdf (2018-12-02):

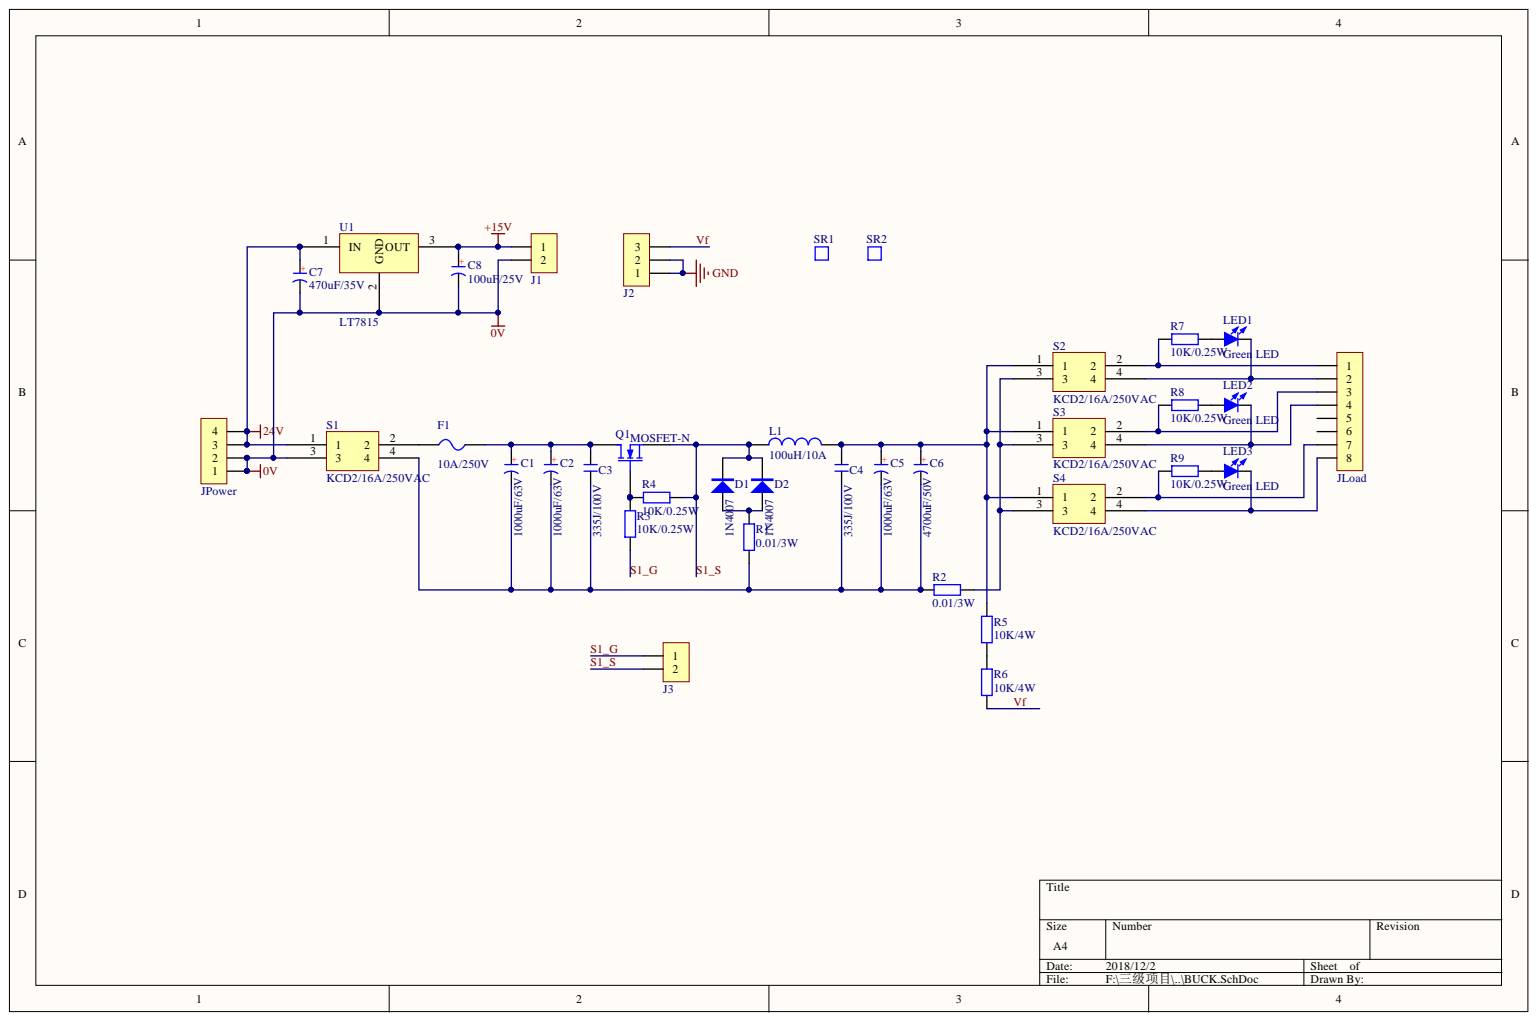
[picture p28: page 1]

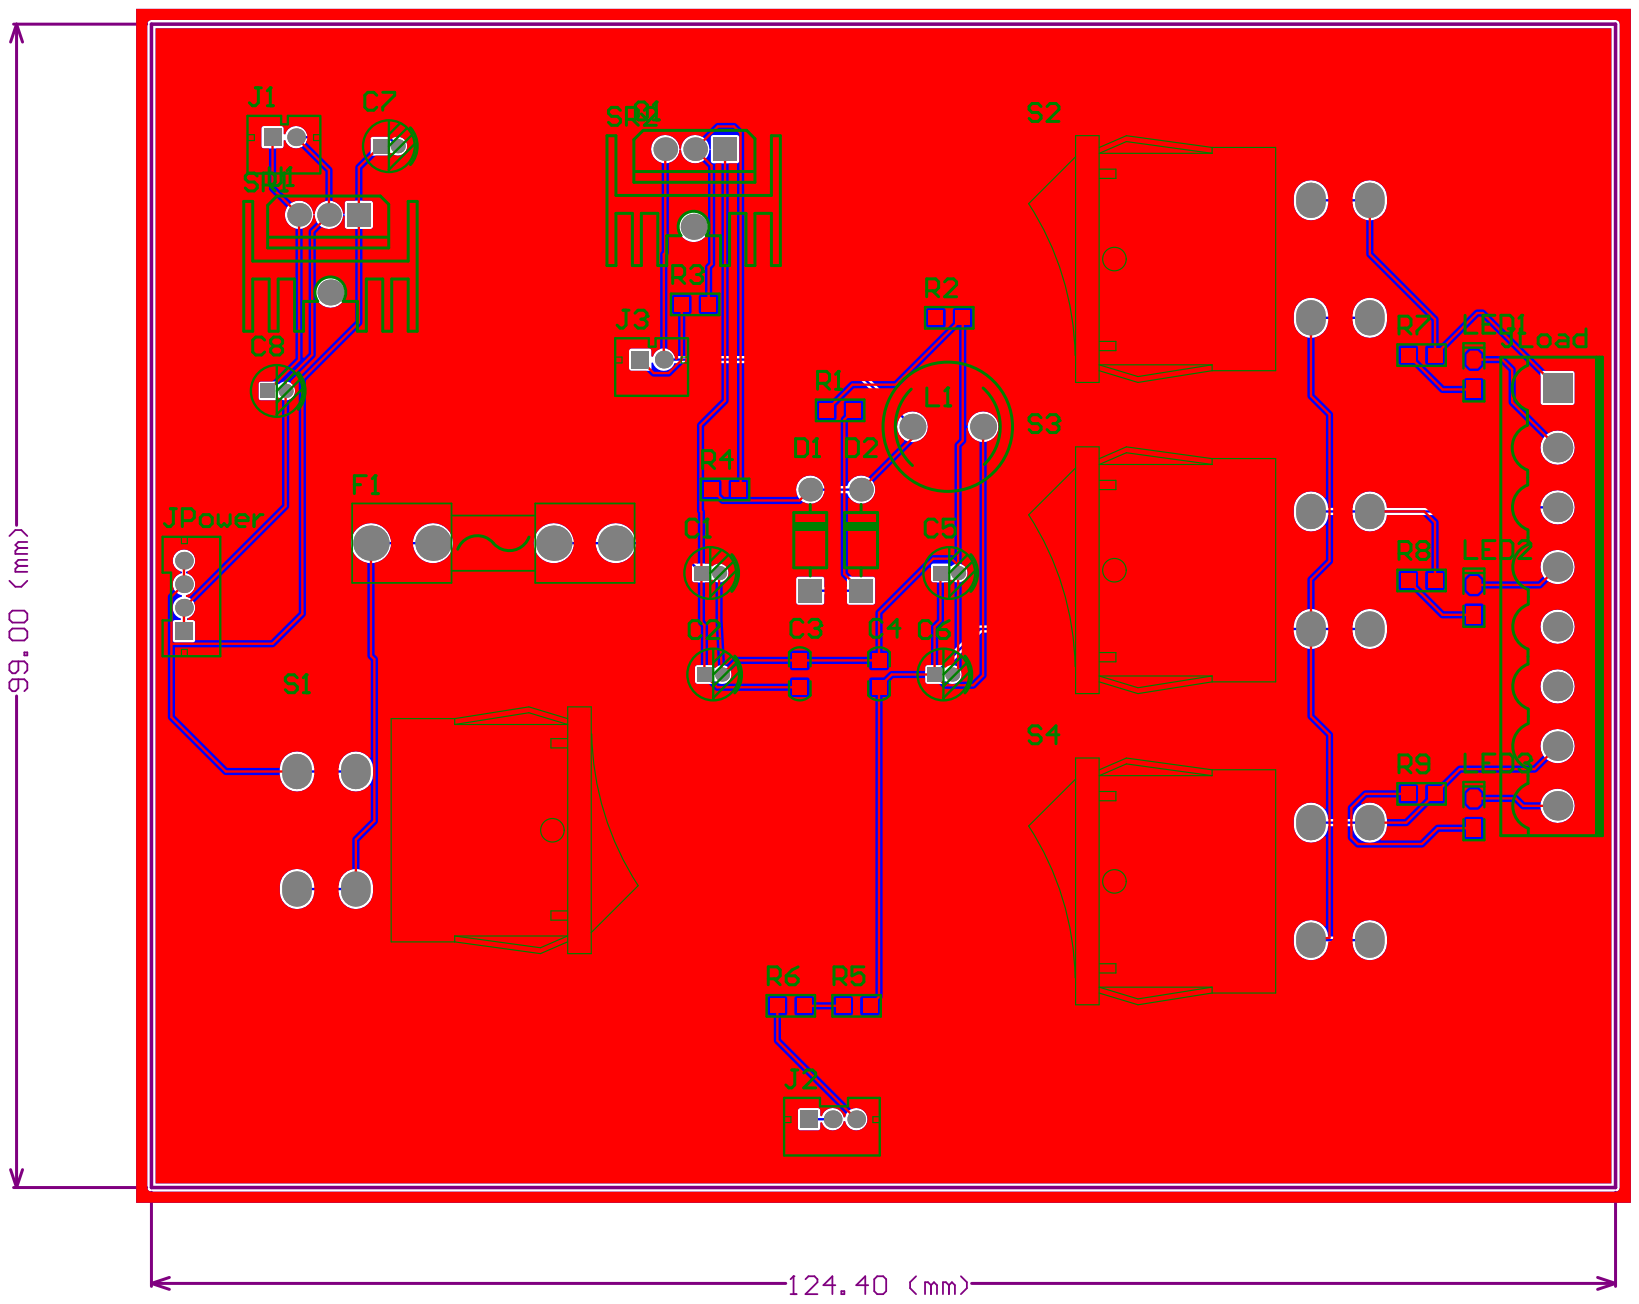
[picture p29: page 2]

Comment | Description | Designator | Footprint | LibRef | Quantity
1000uF/63V | 直插电解电容 | C1, C2, C5 | CAP 1.5*4*8 | C-CAP | 3
335J/100V | 无极性贴片电容 | C3, C4 | C 0805 | C | 2
4700uF/50V | 直插电解电容 | C6 | CAP 1.5*4*8 | C-CAP | 1
470uF/35V | 直插电解电容 | C7 | CAP 1.5*4*8 | C-CAP | 1
100uF/25V | 直插电解电容 | C8 | CAP 1.5*4*8 | C-CAP | 1
1N4007 | 整流二极管 | D1, D2 | DO-41 | 1N4007 | 2
10A/250V | 5*20保险丝 | F1 | FU 5x20 | FU 5x20 | 1
HDR-1X2 | 2P接插件 | J1, J3 | PH2.0 D-L-2P | Header 2 | 2
HDR-1X3 | 3P接插件 | J2 | PH2.0 D-L-3P | Header 3 | 1
HDR-1X8 | 8P接插件 | JLoad | KF2EDGK5.08-8P | Header 8 | 1
HDR-1X4 | 4P接插件 | JPower | PH2.0 D-L-4P | Header 4 | 1
100uH/10A | 小功率贴片电感 | L1 | L 0805 | L | 1
Green LED | 贴片LED | LED1, LED2, LED3 | LED 0805G | LED-SMD | 3
MOSFET-N | N-Channel MOSFET | Q1 | TO220A | MOSFET-N | 1
0.01/3W | 贴片电阻 | R1, R2 | R 0805 | R | 2
10K/0.25W | 贴片电阻 | R3, R4, R7, R8, R9 | R 0805 | R | 5
10K/4W | 贴片电阻 | R5, R6 | R 0805 | R | 2
KCD2/16A/250VAC | | S1, S2, S3, S4 | KCD1-104-W | KCD2/16A/250VAC | 4
散热片 | 散热片 | SR1, SR2 | 散热片 | S1 | 2
LT7815 | | U1 | TO220A | LT7815 | 1

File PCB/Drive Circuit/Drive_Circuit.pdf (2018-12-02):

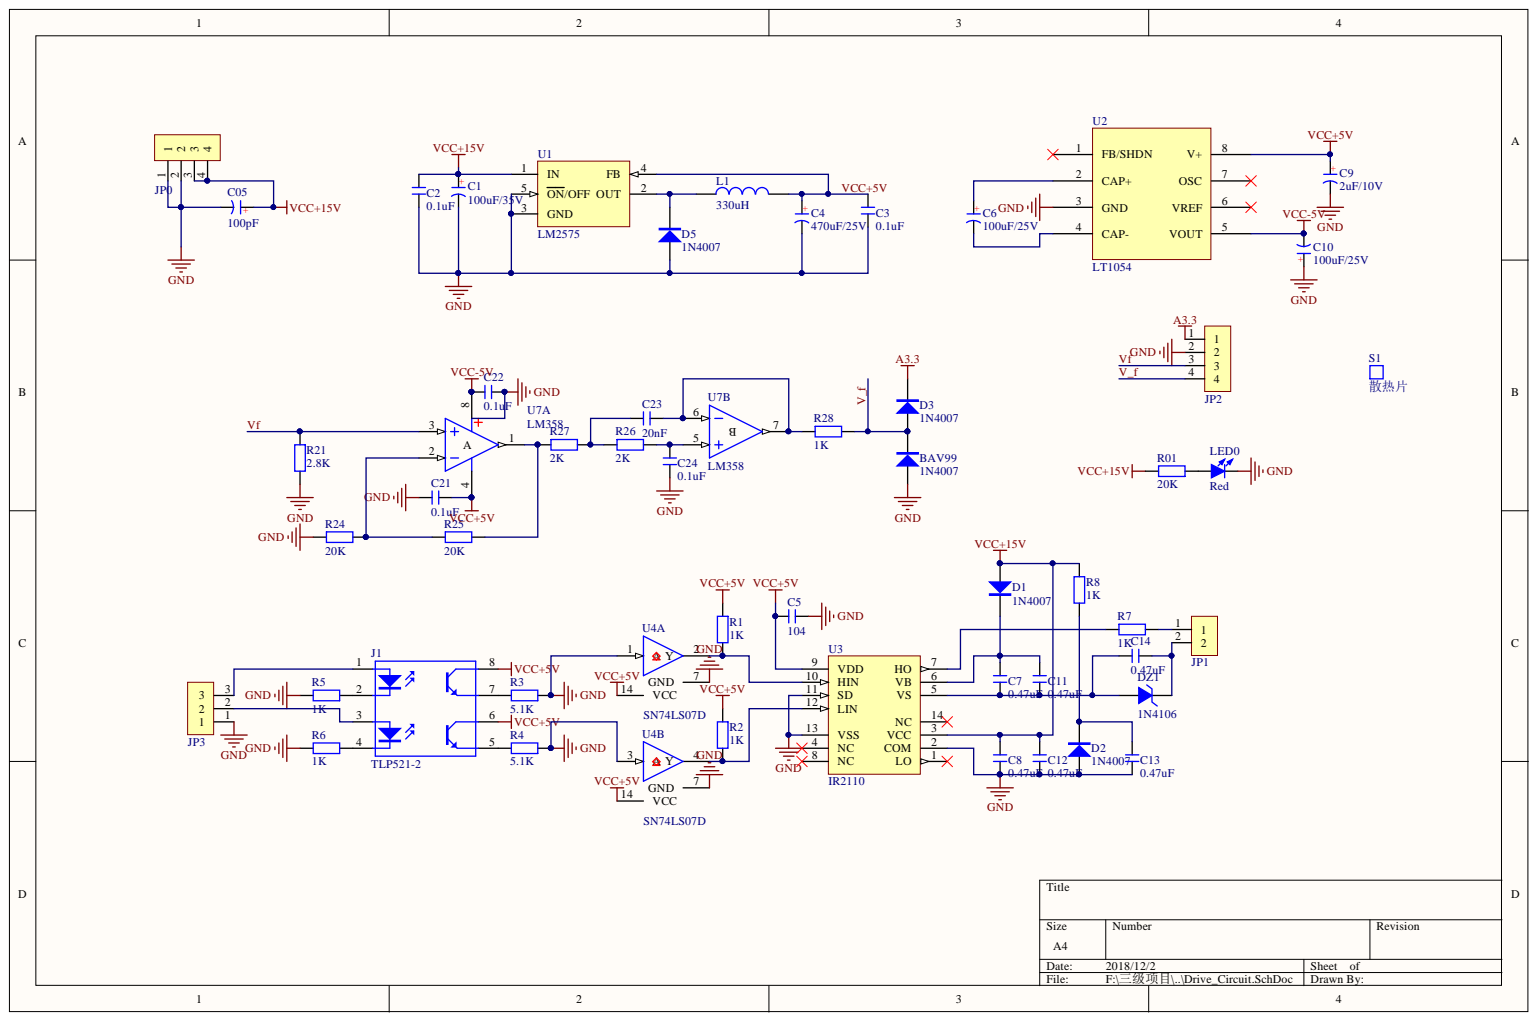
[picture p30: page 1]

ON/OFF 5 | L1

GND 3

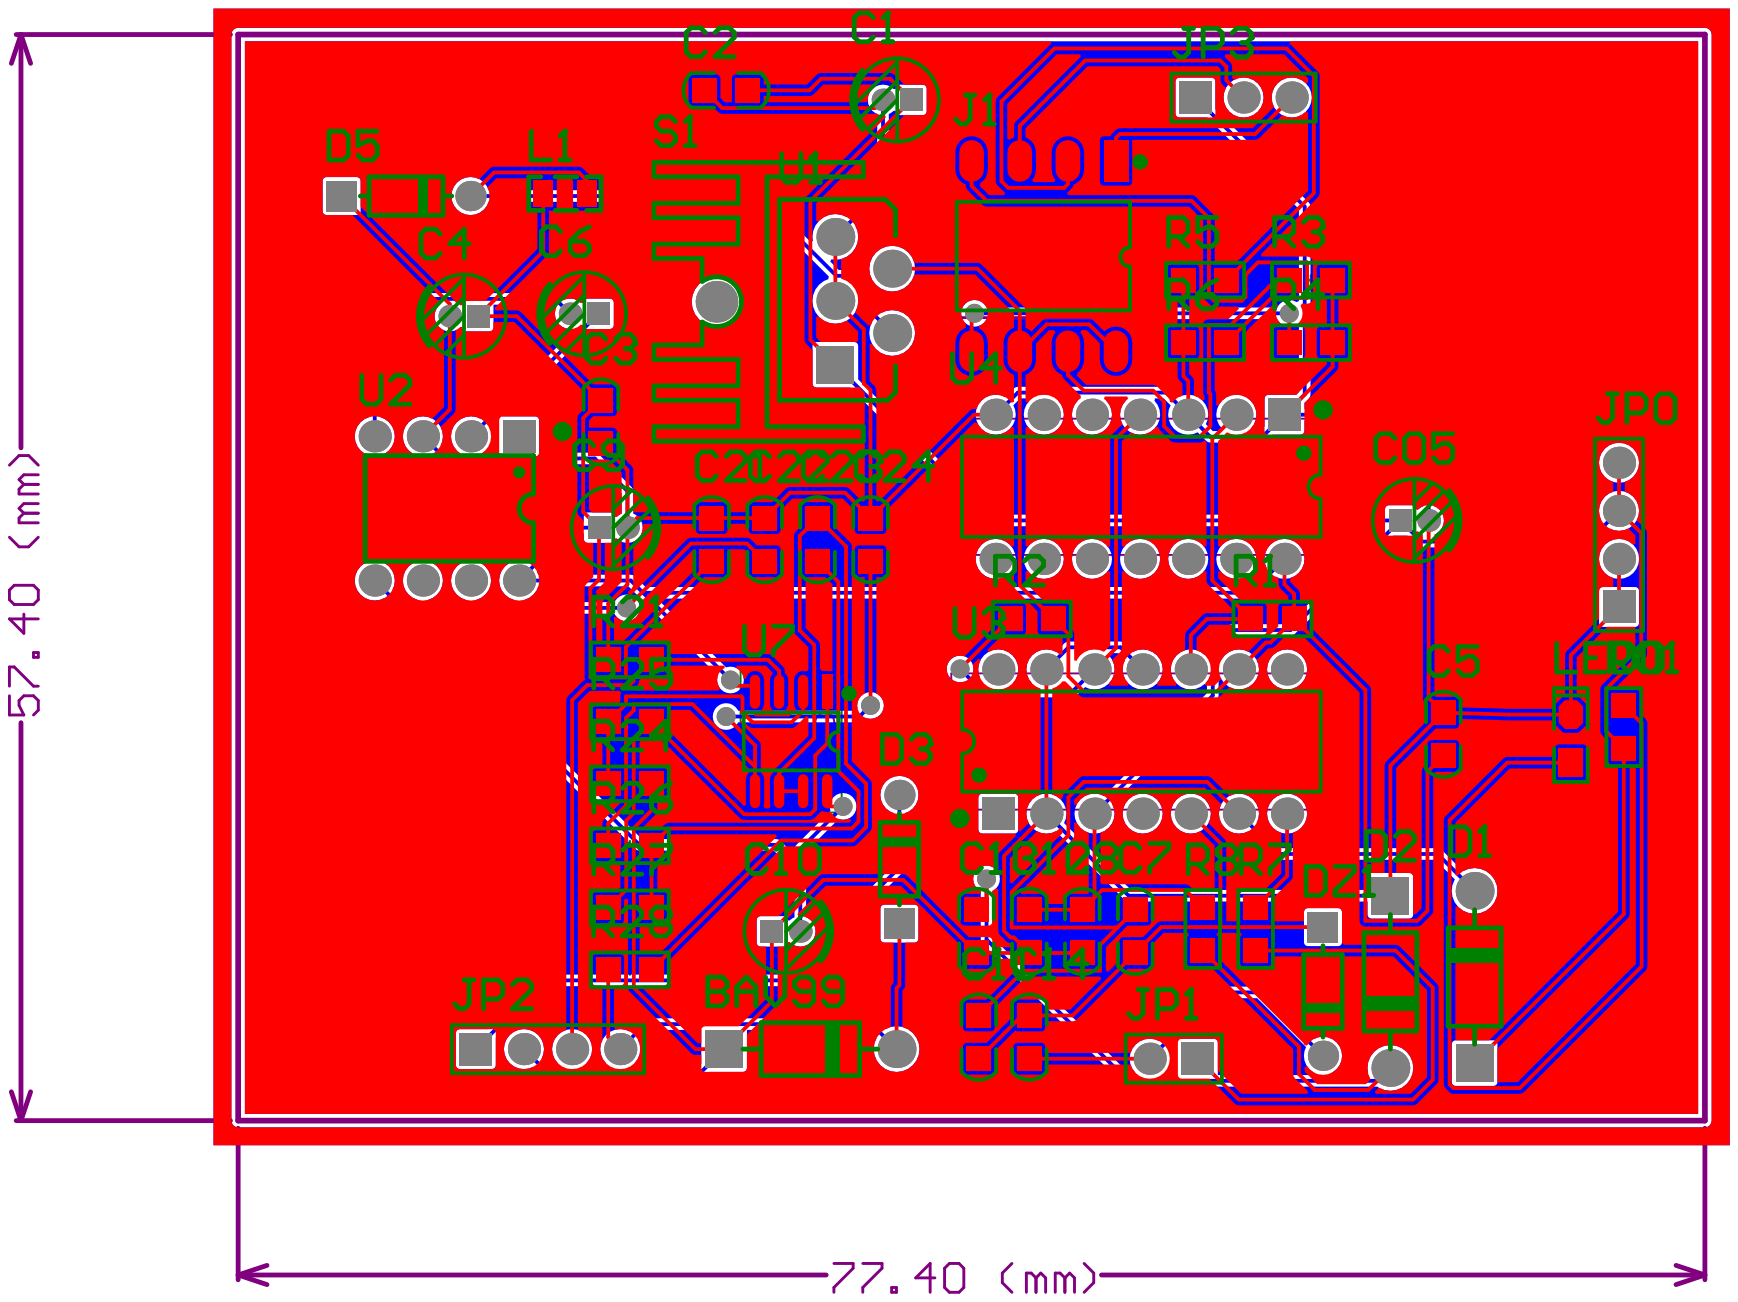
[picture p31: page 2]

Comment | Description | Designator | Footprint | LibRef | Quantity
1N4007 | 整流二极管 | BAV99, D1, D2 | DO-41 | 1N4007 | 3
100uF/35V | 直插电解电容 | C1 | CAP 1.5*4*8 | C-CAP | 1
0.1uF | 无极性贴片电容 | C2, C3, C21, C22, C24 | C 0805 | C | 5
470uF/25V | 直插电解电容 | C4 | CAP 1.5*4*8 | C-CAP | 1
100pF | 直插电解电容 | C05 | CAP 1.5*4*8 | C-CAP | 1
104 | 无极性贴片电容 | C5 | C 0805 | C | 1
100uF/25V | 直插电解电容 | C6, C10 | CAP 1.5*4*8 | C-CAP | 2
0.47uF | 无极性贴片电容 | C7, C8, C11, C12, C13, C14 | C 0805 | C | 6
2uF/10V | 直插电解电容 | C9 | CAP 1.5*4*8 | C-CAP | 1
20nF | 无极性贴片电容 | C23 | C 0805 | C | 1
1N4007 | 整流二极管 | D3, D5 | DO-35 | 1N4007 | 2
1N4106 | 12V/0.5W稳压管 | DZ1 | DO-35 | 1N4106 | 1
TLP521-2 | 2路开关光耦 | J1 | SOP8-W2.54_N | TLP521-2 | 1
HDR-1X4 | 4P接插件 | JP0, JP2 | HDR-1X4 | Header 4 | 2
HDR-1X2 | 2P接插件 | JP1 | HDR-1X2 | Header 2 | 1
HDR-1X3 | 3P接插件 | JP3 | HDR-1X3 | Header 3 | 1
330uH | 小功率贴片电感 | L1 | L 0805 | L | 1
Red | 贴片LED | LED0 | LED 0805G | LED-SMD | 1
1K | 贴片电阻 | R1, R2, R5, R6, R7, R8, R28 | R 0805 | R | 7
20K | 贴片电阻 | R01, R24, R25 | R 0805 | R | 3
5.1K | 贴片电阻 | R3, R4 | R 0805 | R | 2
2.8K | 贴片电阻 | R21 | R 0805 | R | 1
2K | 贴片电阻 | R26, R27 | R 0805 | R | 2
散热片 | 散热片 | S1 | 散热片 | S1 | 1
LM2575 | DC降压芯片 | U1 | TO220-5B | LM2576 | 1
LT1054 | | U2 | DIP8-300 | LT1054 | 1
IR2110 | High and Low Side Driver | U3 | DIP14-300 | IR2110 | 1
SN74LS07D | Hex Buffer / Driver with Open-Collector High-Voltage Outputs | U4 | DIP14-300 | SN74LS07D | 1
LM358 | 双路运放 | U7 | SOP8_N | LM358 | 1

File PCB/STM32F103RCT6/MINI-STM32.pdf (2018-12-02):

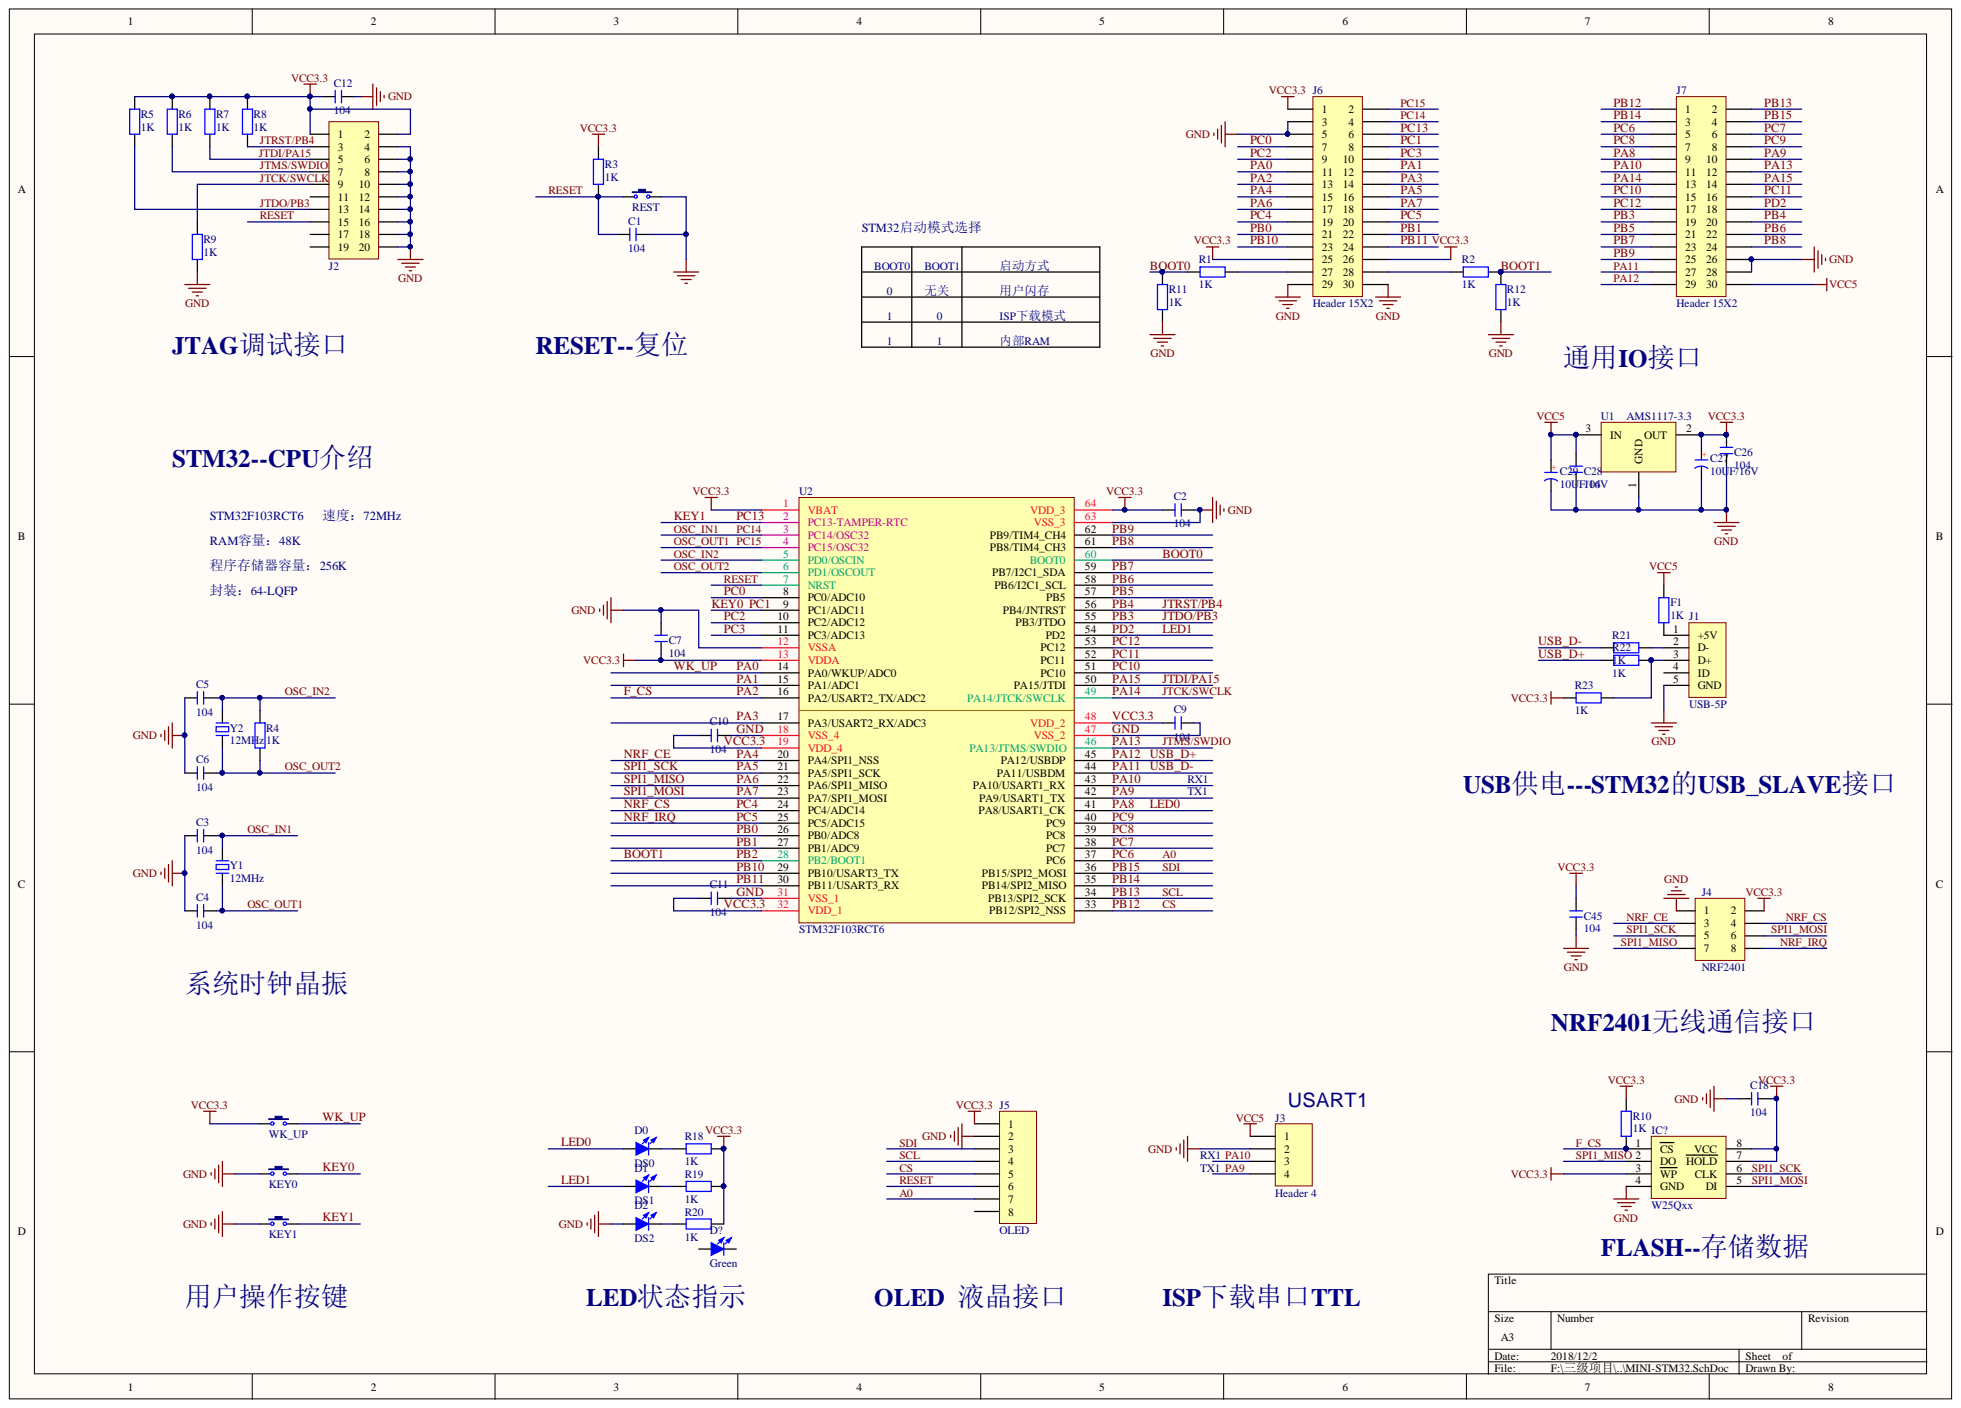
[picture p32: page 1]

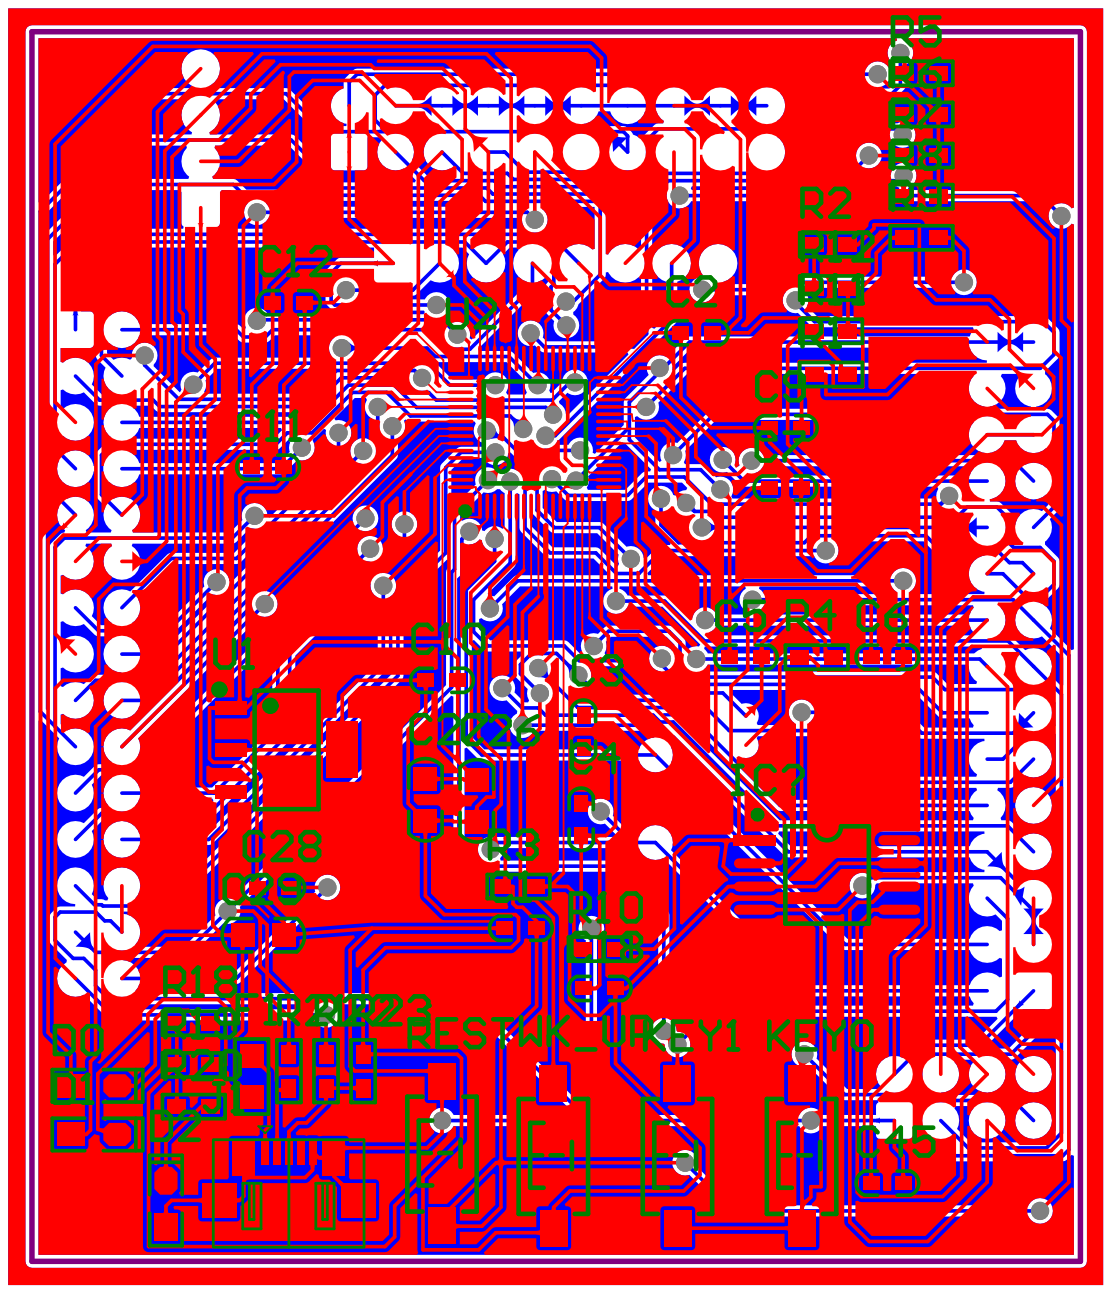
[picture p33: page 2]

Designator | Footprint | Quantity | Comment
C1, C2, C3, C4, C5, C6, C7, C9, C10, C11, C12, C18, C28, C45 | C 0603 | 14 104
C26 | C 0805 | 1 | 104
C27, C29 | C 0805 | 2 10UF/16V
D0 | LED 0805G | 1 | DS0
D1 | LED 0805G | 1 | DS1
D2 | LED 0805G | 1 | DS2
D? | LED 0805G | 1 | Green
F1 | R 0805 | 1 | 1K
IC? | SOP8W_N | 1 | W25Qxx
J1 | USB-MICRO_A | 1 | USB-5P
J2 | HDR-10X2 | 1 | Header 2X10
J3 | HDR-1X4 | 1 | Header 4
J4 | HDR-4X2 | 1 | NRF2401
J5 | HDR-1X8_M | 1 | OLED
J6, J7 | HDR-15X2 | 2 Header 15X2
KEY0, KEY1, REST, WK_UP | TSW SMD-3*6*2.5 | 4 3x6x5
R1, R2, R3, R4, R5, R6, R7, R8, R9, R10, R11, R12, R18, R19, R20, R21, R22, R23 | R 0603 | 18 1K
U1 | SOT223_L | 1 | AMS1117-3.3
U2 | LQFP64 7x7_L | 1 | STM32F103RCT6
Y1 | XTAL-49S DIP | 1 | 12MHz
Y2 | XTAL-3X10 | 1 | 12MHz

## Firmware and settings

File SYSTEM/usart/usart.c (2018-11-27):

#include "sys.h"
#include "usart.h"	  
////////////////////////////////////////////////////////////////////////////////// 	 
//如果使用ucos,则包括下面的头文件即可.
#if SYSTEM_SUPPORT_OS
#include "FreeRTOS.h"					//FreeRTOS使用	 	  
#endif
//////////////////////////////////////////////////////////////////////////////////	 
//本程序只供学习使用，未经作者许可，不得用于其它任何用途
//ALIENTEK STM32开发板
//串口1初始化		   
//正点原子@ALIENTEK
//技术论坛:www.openedv.com
//修改日期:2012/8/18
//版本：V1.5
//版权所有，盗版必究。
//Copyright(C) 广州市星翼电子科技有限公司 2009-2019
//All rights reserved
//********************************************************************************
//V1.3修改说明 
//支持适应不同频率下的串口波特率设置.
//加入了对printf的支持
//增加了串口接收命令功能.
//修正了printf第一个字符丢失的bug
//V1.4修改说明
//1,修改串口初始化IO的bug
//2,修改了USART_RX_STA,使得串口最大接收字节数为2的14次方
//3,增加了USART_REC_LEN,用于定义串口最大允许接收的字节数(不大于2的14次方)
//4,修改了EN_USART1_RX的使能方式
//V1.5修改说明
//1,增加了对UCOSII的支持
////////////////////////////////////////////////////////////////////////////////// 	  
 

//////////////////////////////////////////////////////////////////
//加入以下代码,支持printf函数,而不需要选择use MicroLIB	  
#if 1
#pragma import(__use_no_semihosting)             
//标准库需要的支持函数                 
struct __FILE 
{ 
	int handle; 

}; 

FILE __stdout;       
//定义_sys_exit()以避免使用半主机模式    
void _sys_exit(int x) 
{ 
	x = x; 
} 
//重定义fputc函数 
int fputc(int ch, FILE *f)
{      
	while((USART1->SR&0X40)==0);//循环发送,直到发送完毕   
    USART1->DR = (u8) ch;      
	return ch;
}
#endif 

/*使用microLib的方法*/
 /* 
int fputc(int ch, FILE *f)
{
	USART_SendData(USART1, (uint8_t) ch);

	while (USART_GetFlagStatus(USART1, USART_FLAG_TC) == RESET) {}	
   
    return ch;
}
int GetKey (void)  { 

    while (!(USART1->SR & USART_FLAG_RXNE));

    return ((int)(USART1->DR & 0x1FF));
}
*/
 
#if EN_USART1_RX   //如果使能了接收
//串口1中断服务程序
//注意,读取USARTx->SR能避免莫名其妙的错误   	
u8 USART_RX_BUF[USART_REC_LEN];     //接收缓冲,最大USART_REC_LEN个字节.
//接收状态
//bit15，	接收完成标志
//bit14，	接收到0x0d
//bit13~0，	接收到的有效字节数目
u16 USART_RX_STA=0;       //接收状态标记	  
  
void uart_init(u32 bound){
	//GPIO端口设置
	GPIO_InitTypeDef GPIO_InitStructure;
	USART_InitTypeDef USART_InitStructure;
	NVIC_InitTypeDef NVIC_InitStructure;
	 
	RCC_APB2PeriphClockCmd(RCC_APB2Periph_USART1|RCC_APB2Periph_GPIOA, ENABLE);	//使能USART1，GPIOA时钟
  
	//USART1_TX   GPIOA.9
	GPIO_InitStructure.GPIO_Pin = GPIO_Pin_9; //PA.9
	GPIO_InitStructure.GPIO_Speed = GPIO_Speed_50MHz;
	GPIO_InitStructure.GPIO_Mode = GPIO_Mode_AF_PP;	//复用推挽输出
	GPIO_Init(GPIOA, &GPIO_InitStructure);//初始化GPIOA.9
   
	//USART1_RX	  GPIOA.10初始化
	GPIO_InitStructure.GPIO_Pin = GPIO_Pin_10;//PA10
	GPIO_InitStructure.GPIO_Mode = GPIO_Mode_IN_FLOATING;//浮空输入
	GPIO_Init(GPIOA, &GPIO_InitStructure);//初始化GPIOA.10  

	//Usart1 NVIC 配置
	NVIC_InitStructure.NVIC_IRQChannel = USART1_IRQn;
	NVIC_InitStructure.NVIC_IRQChannelPreemptionPriority=3 ;//抢占优先级3
	NVIC_InitStructure.NVIC_IRQChannelSubPriority = 3;		//子优先级3
	NVIC_InitStructure.NVIC_IRQChannelCmd = ENABLE;			//IRQ通道使能
	NVIC_Init(&NVIC_InitStructure);	//根据指定的参数初始化VIC寄存器
  
	//USART 初始化设置

	USART_InitStructure.USART_BaudRate = bound;//串口波特率
	USART_InitStructure.USART_WordLength = USART_WordLength_8b;//字长为8位数据格式
	USART_InitStructure.USART_StopBits = USART_StopBits_1;//一个停止位
	USART_InitStructure.USART_Parity = USART_Parity_No;//无奇偶校验位
	USART_InitStructure.USART_HardwareFlowControl = USART_HardwareFlowControl_None;//无硬件数据流控制
	USART_InitStructure.USART_Mode = USART_Mode_Rx | USART_Mode_Tx;	//收发模式

	USART_Init(USART1, &USART_InitStructure); //初始化串口1
	USART_ITConfig(USART1, USART_IT_RXNE, ENABLE);//开启串口接受中断
	USART_Cmd(USART1, ENABLE);                    //使能串口1 
}

void USART1_IRQHandler(void)                	//串口1中断服务程序
{
	u8 Res;

	if(USART_GetITStatus(USART1, USART_IT_RXNE) != RESET)  //接收中断(接收到的数据必须是0x0d 0x0a结尾)
		{
		Res =USART_ReceiveData(USART1);	//读取接收到的数据
		
		if((USART_RX_STA&0x8000)==0)//接收未完成
			{
			if(USART_RX_STA&0x4000)//接收到了0x0d
				{
				if(Res!=0x0a)USART_RX_STA=0;//接收错误,重新开始
				else USART_RX_STA|=0x8000;	//接收完成了 
				}
			else //还没收到0X0D
				{	
				if(Res==0x0d)USART_RX_STA|=0x4000;
				else
					{
					USART_RX_BUF[USART_RX_STA&0X3FFF]=Res ;
					USART_RX_STA++;
					if(USART_RX_STA>(USART_REC_LEN-1))USART_RX_STA=0;//接收数据错误,重新开始接收	  
					}		 
				}
			}   		 
     } 
} 
#endif	

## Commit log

2018-11-28 pwm adjustment
2018-11-30 Init PCB Project
    [MINI-STM32.PRJPCB, MINI-STM32.PcbLib, MINI-STM32.SchDoc]
2018-11-30 Create Device Circuit PCB
    [Drive_Circuit.PrjPcb, Drive_Circuit.SchDoc, LT1054.SchLib]
2018-12-02 Creat BUCK Circuit and perfect Readme.md
    [BUCK.PcbDoc, BUCK.PrjPcb, BUCK.SchDoc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]

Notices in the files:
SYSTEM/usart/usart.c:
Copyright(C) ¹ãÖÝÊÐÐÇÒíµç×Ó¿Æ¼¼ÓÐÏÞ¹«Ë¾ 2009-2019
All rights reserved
